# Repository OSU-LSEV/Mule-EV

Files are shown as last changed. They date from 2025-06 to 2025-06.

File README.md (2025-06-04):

# Mule-EV
Modified iteration of the woodpecker EV platform 

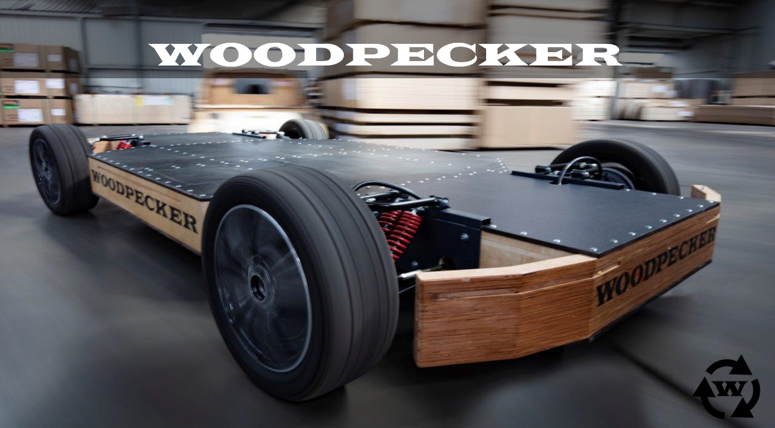
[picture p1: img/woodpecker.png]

# Woodpecker 
## Design documentation and Operating Manual
The main information backboan is CAN bus.

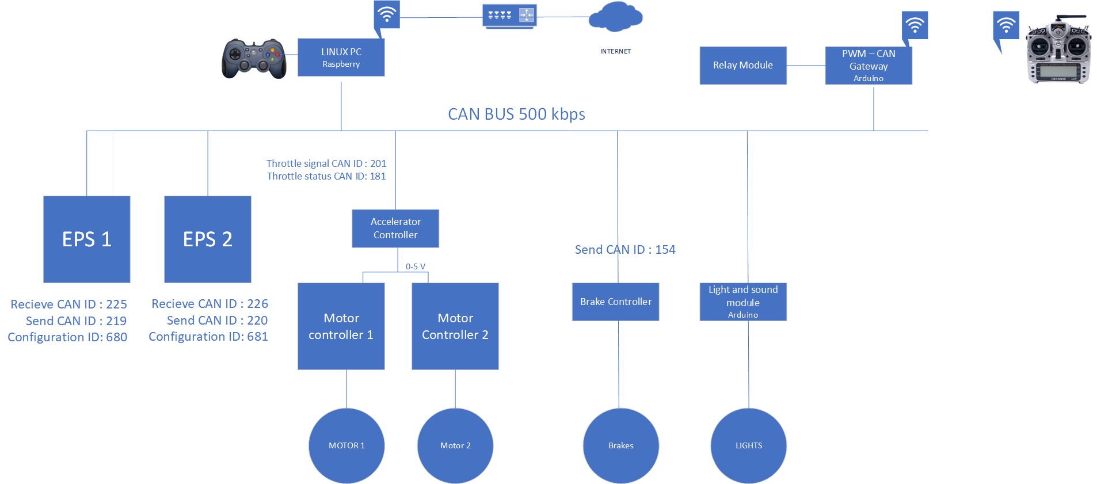
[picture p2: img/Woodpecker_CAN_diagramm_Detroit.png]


# Operation
There are 2 operating modes: manual and DbW mode. 
Wireless operations:

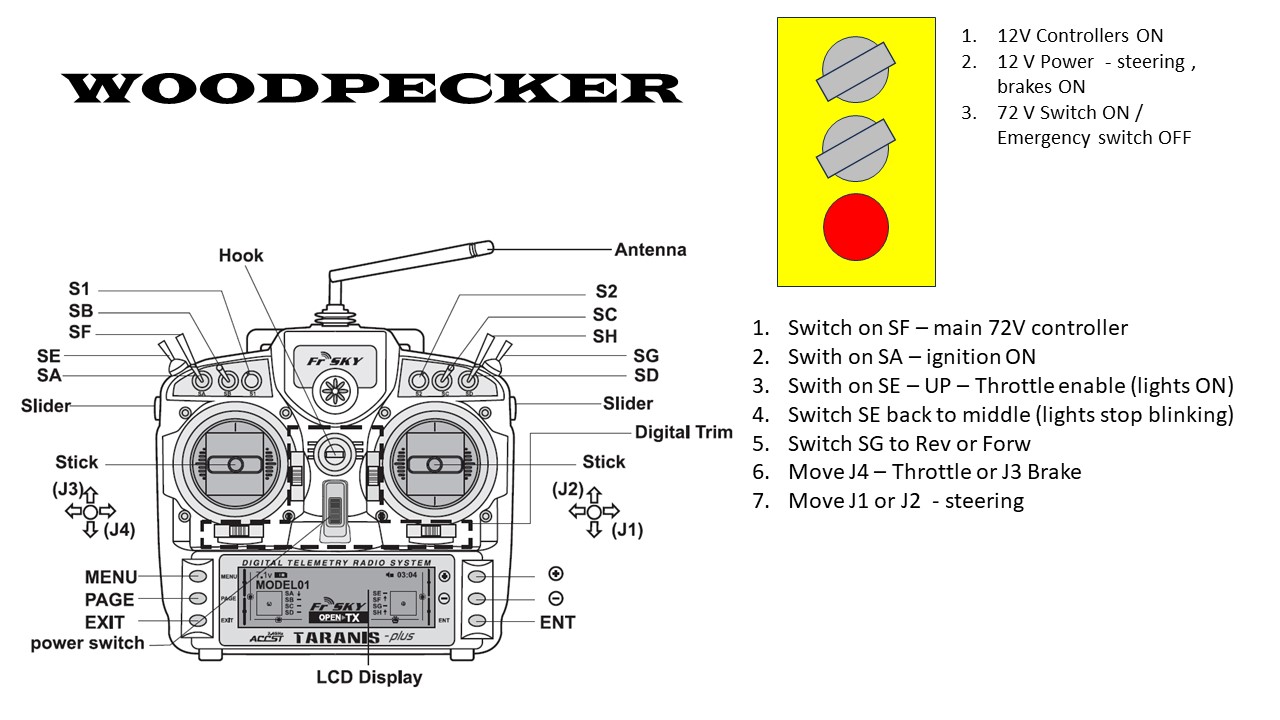
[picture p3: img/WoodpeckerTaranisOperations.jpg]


## Switching ON DbW mode

1. Switch DbW ON switch on front panel. Red signal light must light on. [Make sure mushroom Emergency STOP is released]
2. Wait for 30-50 sec to boot up Joystick micro computer. Joystick demo application should startup automatically.
3. Press START on joystick controller [Should hear clicking noise of controller relays] to enable controller.
4. Press Y to switch on ignition. Wait for 2-3 sec.
5. Press B to start starter.
6. Use joystick controls to drive, manually switch into high or low gear.

# Main DbW components.

Drive By Wire system consists from:

**1. Accelerator Controller**

Connected to motor controller. Receive commands and provide report via DbW CAN messages. Located in Rigt side. 

**2. Brake Controller.**

Connected to hydraulic brake unit. Receive commands and provide report via DbW CAN messages. Located in Middle

**3. Control Processor.**

Control processor is connected to DbW CAN network and 4 relay block and 2 push button switches to provide Engine ON, OFF and override functionality. Located in Right side 

**4. Joystick micro computer**

Raspberry Pi micro computer is located in Right side of vehicle, Logitech F310 gamepad attached via USB port. Connected to DbW CAN and LAN port on front panel. Joystick sample application is located on microcomputer dir /home/pi/Razor .
Bash script fro automatic joystick launch is located @ /home/pi/dbwstart.sh
Script is being launched on bootup from config file /etc/rc.local

content of .dbstart.sh script:
```
#!/bin/bash

sudo ip link set can0 type can bitrate 500000
sudo ip link set up can0
sudo ip link set can1 type can bitrate 500000
sudo ip link set up can1
cd /home/pi/Razor/build
./oscc-joystick-commander 0
```

Access information:
```
Connect using SSH to 10.0.10.15:22
User: pi
Password: nvidia
```

# CAN buse
There are 1 CAN buses on vehicle. DbW CAN screw terminal is located in Right side.

1. DbW CAN bus. - 500k

Connected devices: Brake controller, Accelerator controller, Steering controller, CAN Gateway, 

# Controls

1. DbW ON - Main Power switch ON/OFF. Power up all controllers. If Switched OFF DbW is disabled, fall back to manual.
2. Emergency STOP - DbW switch off. If pressed, DbW controls disabled, switch back to manual mode. Connected in Parallel with DbW ON switch.
3. LAN Connection - LAN port to connect to Joystick micro computer.
4. Power Steer ON - Button to force steering unit to switch ON power assist mode.

## Joystick operation

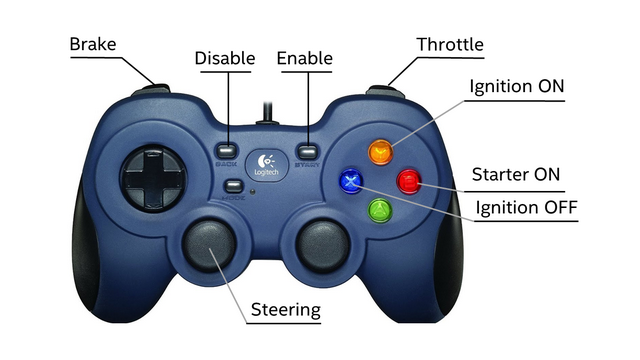
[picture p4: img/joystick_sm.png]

```
START - Enable controls
BACK - Disable controls
LEFT TRIGGER - Brake
RIGHT TRIGGER - Throttle
LEFT STICK - Steering
Y - Ignition ON
X - Ignition OFF
B - Starter ON
```
## CAN Modem

System is using PEAK CAN USB modem.
Drivers are available from Peak Systems website : https://www.peak-system.com/PCAN-USB.199.0.html?L=1# 
Connection port connector is located in the front panel of 
Pin out diagram is here:

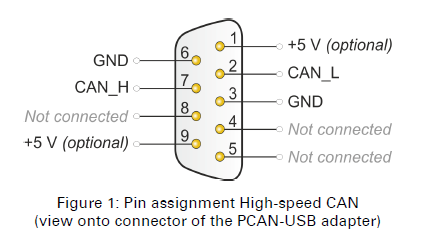
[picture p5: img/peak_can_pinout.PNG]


# Operation from management computer with joystick application:

In order to start operations of DbW:

1.	Switch main power switch On.
2.	Wait 1-2 min to start all processors.
3.	Initiate joystick controller (for test mode only). Connect to DbW GW controller from management PC:
a.	Launch Putty;
b.	Enter SSH connection to 10.0.10.15 
c.	Launch 1st  test window to monitor accelerator/braking signal:
d.	Enter username : pi
e.	Enter password: nvidia

```
cd /home/pi/can-utils
./candump can1
```
f.	As result the realtime changing data should appear:
```
  can1  061   [8]  05 CC 01 00 00 0F 00 01
  can1  063   [8]  05 CC 01 00 00 F2 08 08
  can1  061   [8]  05 CC 01 00 00 0F 00 01
  can1  063   [8]  05 CC 01 00 00 40 02 06
```

If there are no realtime data – DbW CAN interface is down, See troubleshooting.

k.	Launch 2nd Putty Window for joystick commander: 
cd /home/pi/Razor/build
./oscc-joystick-commander 0       

l.	There should be visible initiating screen – similar to: 
```
Opening EPAS CAN channel: can0
Opening CAN channel: can1
Found 1 devices -- connecting to device at system index 0 - GUID:030000006d0400001dc2000014400000
Waiting for joystick controls to zero
Joystick controls successfully initialized

Control Ready:
    START - Enable controls
    BACK - Disable controls
    LEFT TRIGGER - Brake
    RIGHT TRIGGER - Throttle
    LEFT STICK - Steering
```
m.	Press “START” to Enable controls, press “BACK” to Disable controls
n.	Controls on Joystick:     LEFT TRIGGER – Brake; RIGHT TRIGGER – Throttle ; LEFT STICK - Steering
o.	Typical view of DbW interface:
```
Brake: 0.000000 Throttle: 0.950990 Steering bytes: 0000
Brake: 0.000000 Throttle: 0.920007 Steering bytes: 0000
```
4.	Switch on ignition.
5.  Start the Engine
5.	Manually switch in to gear
7.	Start driving with joystick control

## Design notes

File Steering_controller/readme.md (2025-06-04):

# Woodpecker 
## Steering controller

PILOT SBW2 EPS is Drive-by-wire electric power steering (EPS) system

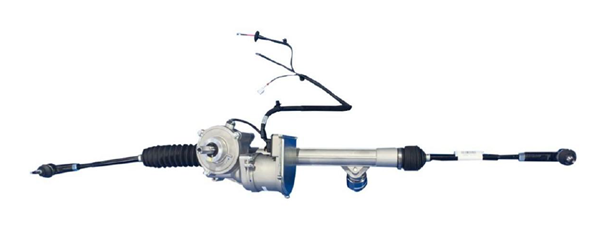
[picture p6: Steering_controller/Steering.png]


Steering module is used to convert CAN message to steering angle.
Module is configured to operate on 500Kbps baudrate.

The message is used in: https://github.com/OSU-LSEV/Mule-EV/blob/main/PWM_CAN_gateway/Woodpecker_PWM_CAN_GTW_Oregon/Woodpecker_PWM_CAN_GTW_Oregon.ino

Mapping of important CAN commandes from CAN .dbc files : https://bitbucket.org/pilotautomotive/woodpecker-detroit-documentation/src/master/CAN_docs/Woodpecker_Detroit.DBF  
```
StatusEPS1: 0x225
StatusEPS2: 0x226
CommandEPS1: 0x219
CommandEPS2: 0x220

```
Calculations of steering applied as CAN DEC to HEX messages are here: https://github.com/OSU-LSEV/Mule-EV/blob/main/Steering_controller/EPS_CAN_messages_calculation.xlsx and here https://github.com/OSU-LSEV/Mule-EV/blob/main/Steering_controller/Steering_joystick_commands.xlsx 
The final predifined messages from https://github.com/OSU-LSEV/Mule-EV/blob/main/PWM_CAN_gateway/Woodpecker_PWM_CAN_GTW_Oregon/Woodpecker_PWM_CAN_GTW_Oregon.ino  remote control look like:
```
unsigned char steer20[8] = {0x40, 0xFA, 0xCF, 0x39, 0x00, 0x00, 0x00, 0x00};
unsigned char steer19[8] = {0x40, 0xFA, 0x71, 0x38, 0x00, 0x00, 0x00, 0x00};
unsigned char steer18[8] = {0x40, 0xFA, 0x13, 0x37, 0x00, 0x00, 0x00, 0x00};
unsigned char steer17[8] = {0x40, 0xFA, 0xB5, 0x35, 0x00, 0x00, 0x00, 0x00};
unsigned char steer16[8] = {0x40, 0xFA, 0x57, 0x34, 0x00, 0x00, 0x00, 0x00};
unsigned char steer15[8] = {0x40, 0xFA, 0xF9, 0x32, 0x00, 0x00, 0x00, 0x00};
unsigned char steer14[8] = {0x40, 0xFA, 0x9B, 0x31, 0x00, 0x00, 0x00, 0x00};
unsigned char steer13[8] = {0x40, 0xFA, 0x3D, 0x30, 0x00, 0x00, 0x00, 0x00};
unsigned char steer12[8] = {0x40, 0xFA, 0xDF, 0x2E, 0x00, 0x00, 0x00, 0x00};
unsigned char steer11[8] = {0x40, 0xFA, 0x81, 0x2D, 0x00, 0x00, 0x00, 0x00};
unsigned char steer10[8] = {0x40, 0xFA, 0x23, 0x2C, 0x00, 0x00, 0x00, 0x00};
unsigned char steer9[8] = {0x40, 0xFA, 0xC5, 0x2A, 0x00, 0x00, 0x00, 0x00};
unsigned char steer8[8] = {0x40, 0xFA, 0x67, 0x29, 0x00, 0x00, 0x00, 0x00};
unsigned char steer7[8] = {0x40, 0xFA, 0x09, 0x28, 0x00, 0x00, 0x00, 0x00};
unsigned char steer6[8] = {0x40, 0xFA, 0xAB, 0x26, 0x00, 0x00, 0x00, 0x00};
unsigned char steer5[8] = {0x40, 0xFA, 0x4D, 0x25, 0x00, 0x00, 0x00, 0x00};
unsigned char steer4[8] = {0x40, 0xFA, 0xEF, 0x23, 0x00, 0x00, 0x00, 0x00};
unsigned char steer3[8] = {0x40, 0xFA, 0x91, 0x22, 0x00, 0x00, 0x00, 0x00};
unsigned char steer2[8] = {0x40, 0xFA, 0x33, 0x21, 0x00, 0x00, 0x00, 0x00};
unsigned char steer1[8] = {0x40, 0xFA, 0xD5, 0x1F, 0x00, 0x00, 0x00, 0x00};
unsigned char steer0[8] = {0x40, 0xFA, 0x77, 0x1E, 0x00, 0x00, 0x00, 0x00};
unsigned char steern1[8] = {0x40, 0xFA, 0x19, 0x1D, 0x00, 0x00, 0x00, 0x00};
unsigned char steern2[8] = {0x40, 0xFA, 0xBB, 0x1B, 0x00, 0x00, 0x00, 0x00};
unsigned char steern3[8] = {0x40, 0xFA, 0x5D, 0x1A, 0x00, 0x00, 0x00, 0x00};
unsigned char steern4[8] = {0x40, 0xFA, 0xFF, 0x18, 0x00, 0x00, 0x00, 0x00};
unsigned char steern5[8] = {0x40, 0xFA, 0xA1, 0x17, 0x00, 0x00, 0x00, 0x00};
unsigned char steern6[8] = {0x40, 0xFA, 0x43, 0x16, 0x00, 0x00, 0x00, 0x00};
unsigned char steern7[8] = {0x40, 0xFA, 0xE5, 0x14, 0x00, 0x00, 0x00, 0x00};
unsigned char steern8[8] = {0x40, 0xFA, 0x87, 0x13, 0x00, 0x00, 0x00, 0x00};
unsigned char steern9[8] = {0x40, 0xFA, 0x29, 0x12, 0x00, 0x00, 0x00, 0x00};
unsigned char steern10[8] = {0x40, 0xFA, 0xCB, 0x10, 0x00, 0x00, 0x00, 0x00};
unsigned char steern11[8] = {0x40, 0xFA, 0x6D, 0x0F, 0x00, 0x00, 0x00, 0x00};
unsigned char steern12[8] = {0x40, 0xFA, 0x0F, 0x0E, 0x00, 0x00, 0x00, 0x00};
unsigned char steern13[8] = {0x40, 0xFA, 0xB1, 0x0C, 0x00, 0x00, 0x00, 0x00};
unsigned char steern14[8] = {0x40, 0xFA, 0x53, 0x0B, 0x00, 0x00, 0x00, 0x00};
unsigned char steern15[8] = {0x40, 0xFA, 0xF5, 0x09, 0x00, 0x00, 0x00, 0x00};
unsigned char steern16[8] = {0x40, 0xFA, 0x97, 0x08, 0x00, 0x00, 0x00, 0x00};
unsigned char steern17[8] = {0x40, 0xFA, 0x38, 0x07, 0x00, 0x00, 0x00, 0x00};
unsigned char steern18[8] = {0x40, 0xFA, 0xDA, 0x05, 0x00, 0x00, 0x00, 0x00};
unsigned char steern19[8] = {0x40, 0xFA, 0x7C, 0x04, 0x00, 0x00, 0x00, 0x00};
unsigned char steern20[8] = {0x40, 0xFA, 0x1E, 0x03, 0x00, 0x00, 0x00, 0x00};
```

and

```
if (ch1 > 980 && ch1 < 1105) {CAN.sendMsgBuf(0x219, 0, 8, steern20);Serial.println(-20);};
  if (ch1 > 1106 && ch1 < 1125) {CAN.sendMsgBuf(0x219, 0, 8, steern19);Serial.println(-19);};
  if (ch1 > 1126 && ch1 < 1145) {CAN.sendMsgBuf(0x219, 0, 8, steern18);Serial.println(-18);};
  if (ch1 > 1146 && ch1 < 1165) {CAN.sendMsgBuf(0x219, 0, 8, steern17);Serial.println(-17);};
  if (ch1 > 1166 && ch1 < 1185) {CAN.sendMsgBuf(0x219, 0, 8, steern16);Serial.println(-16);};
  if (ch1 > 1186 && ch1 < 1205) {CAN.sendMsgBuf(0x219, 0, 8, steern15);Serial.println(-15);};
  if (ch1 > 1206 && ch1 < 1225) {CAN.sendMsgBuf(0x219, 0, 8, steern14);Serial.println(-14);};
  if (ch1 > 1226 && ch1 < 1245) {CAN.sendMsgBuf(0x219, 0, 8, steern13);Serial.println(-13);};
  if (ch1 > 1246 && ch1 < 1265) {CAN.sendMsgBuf(0x219, 0, 8, steern12);Serial.println(-12);};
  if (ch1 > 1266 && ch1 < 1285) {CAN.sendMsgBuf(0x219, 0, 8, steern11);Serial.println(-11);};
  if (ch1 > 1286 && ch1 < 1305) {CAN.sendMsgBuf(0x219, 0, 8, steern10);Serial.println(-10);};
  if (ch1 > 1306 && ch1 < 1325) {CAN.sendMsgBuf(0x219, 0, 8, steern9);Serial.println(-9);};
  if (ch1 > 1326 && ch1 < 1345) {CAN.sendMsgBuf(0x219, 0, 8, steern8);Serial.println(-8);};
  if (ch1 > 1346 && ch1 < 1365) {CAN.sendMsgBuf(0x219, 0, 8, steern7);Serial.println(-7);};
  if (ch1 > 1366 && ch1 < 1385) {CAN.sendMsgBuf(0x219, 0, 8, steern6);Serial.println(-6);};
  if (ch1 > 1386 && ch1 < 1405) {CAN.sendMsgBuf(0x219, 0, 8, steern5);Serial.println(-5);};
  if (ch1 > 1406 && ch1 < 1425) {CAN.sendMsgBuf(0x219, 0, 8, steern4);Serial.println(-4);};
  if (ch1 > 1426 && ch1 < 1445) {CAN.sendMsgBuf(0x219, 0, 8, steern3);Serial.println(-3);};
  if (ch1 > 1446 && ch1 < 1465) {CAN.sendMsgBuf(0x219, 0, 8, steern2);Serial.println(-2);};
  if (ch1 > 1466 && ch1 < 1479) {CAN.sendMsgBuf(0x219, 0, 8, steer0);Serial.println(-1);};
  if (ch1 > 1480 && ch1 < 1505) {CAN.sendMsgBuf(0x219, 0, 8, steer0);Serial.println(0);};
  if (ch1 > 1506 && ch1 < 1525) {CAN.sendMsgBuf(0x219, 0, 8, steer0);Serial.println(1);};
  if (ch1 > 1526 && ch1 < 1545) {CAN.sendMsgBuf(0x219, 0, 8, steer2);Serial.println(2);};
  if (ch1 > 1546 && ch1 < 1565) {CAN.sendMsgBuf(0x219, 0, 8, steer3);Serial.println(3);};
  if (ch1 > 1566 && ch1 < 1585) {CAN.sendMsgBuf(0x219, 0, 8, steer4);Serial.println(4);};
  if (ch1 > 1586 && ch1 < 1605) {CAN.sendMsgBuf(0x219, 0, 8, steer5);Serial.println(5);};
  if (ch1 > 1606 && ch1 < 1625) {CAN.sendMsgBuf(0x219, 0, 8, steer6);Serial.println(6);};
  if (ch1 > 1626 && ch1 < 1645) {CAN.sendMsgBuf(0x219, 0, 8, steer7);Serial.println(7);};
  if (ch1 > 1646 && ch1 < 1665) {CAN.sendMsgBuf(0x219, 0, 8, steer8);Serial.println(8);};
  if (ch1 > 1666 && ch1 < 1685) {CAN.sendMsgBuf(0x219, 0, 8, steer9);Serial.println(9);};
  if (ch1 > 1686 && ch1 < 1705) {CAN.sendMsgBuf(0x219, 0, 8, steer10);Serial.println(10);};
  if (ch1 > 1706 && ch1 < 1725) {CAN.sendMsgBuf(0x219, 0, 8, steer11);Serial.println(11);};
  if (ch1 > 1726 && ch1 < 1745) {CAN.sendMsgBuf(0x219, 0, 8, steer12);Serial.println(12);};
  if (ch1 > 1746 && ch1 < 1765) {CAN.sendMsgBuf(0x219, 0, 8, steer13);Serial.println(13);};
  if (ch1 > 1766 && ch1 < 1785) {CAN.sendMsgBuf(0x219, 0, 8, steer14);Serial.println(14);};
  if (ch1 > 1786 && ch1 < 1805) {CAN.sendMsgBuf(0x219, 0, 8, steer15);Serial.println(15);};
  if (ch1 > 1806 && ch1 < 1825) {CAN.sendMsgBuf(0x219, 0, 8, steer16);Serial.println(16);};
  if (ch1 > 1826 && ch1 < 1845) {CAN.sendMsgBuf(0x219, 0, 8, steer17);Serial.println(17);};
  if (ch1 > 1846 && ch1 < 1865) {CAN.sendMsgBuf(0x219, 0, 8, steer18);Serial.println(18);};
  if (ch1 > 1866 && ch1 < 1885) {CAN.sendMsgBuf(0x219, 0, 8, steer19);Serial.println(19);};
  if (ch1 > 1886 && ch1 < 2005) {CAN.sendMsgBuf(0x219, 0, 8, steer19);Serial.println(20);};

if (ch3 > 1000 && ch3 < 1189) CAN.sendMsgBuf(0x220, 0, 8, steern20);
if (ch3 > 1190 && ch3 < 1209) CAN.sendMsgBuf(0x220, 0, 8, steern19);
if (ch3 > 1210 && ch3 < 1229) CAN.sendMsgBuf(0x220, 0, 8, steern18);
if (ch3 > 1230 && ch3 < 1249) CAN.sendMsgBuf(0x220, 0, 8, steern17);
if (ch3 > 1250 && ch3 < 1269) CAN.sendMsgBuf(0x220, 0, 8, steern16);
if (ch3 > 1270 && ch3 < 1289) CAN.sendMsgBuf(0x220, 0, 8, steern15);
if (ch3 > 1290 && ch3 < 1309) CAN.sendMsgBuf(0x220, 0, 8, steern14);
if (ch3 > 1310 && ch3 < 1329) CAN.sendMsgBuf(0x220, 0, 8, steern13);
if (ch3 > 1330 && ch3 < 1349) CAN.sendMsgBuf(0x220, 0, 8, steern12);
if (ch3 > 1350 && ch3 < 1369) CAN.sendMsgBuf(0x220, 0, 8, steern11);
if (ch3 > 1370 && ch3 < 1389) CAN.sendMsgBuf(0x220, 0, 8, steern10);
if (ch3 > 1390 && ch3 < 1409) CAN.sendMsgBuf(0x220, 0, 8, steern9);
if (ch3 > 1410 && ch3 < 1429) CAN.sendMsgBuf(0x220, 0, 8, steern8);
if (ch3 > 1430 && ch3 < 1449) CAN.sendMsgBuf(0x220, 0, 8, steern7);
if (ch3 > 1450 && ch3 < 1469) CAN.sendMsgBuf(0x220, 0, 8, steern6);
if (ch3 > 1470 && ch3 < 1489) CAN.sendMsgBuf(0x220, 0, 8, steern5);
if (ch3 > 1490 && ch3 < 1509) CAN.sendMsgBuf(0x220, 0, 8, steern4);
if (ch3 > 1510 && ch3 < 1529) CAN.sendMsgBuf(0x220, 0, 8, steern3);
if (ch3 > 1530 && ch3 < 1549) CAN.sendMsgBuf(0x220, 0, 8, steern2);
if (ch3 > 1550 && ch3 < 1569) CAN.sendMsgBuf(0x220, 0, 8, steern1);
if (ch3 > 1570 && ch3 < 1590) CAN.sendMsgBuf(0x220, 0, 8, steer0);
if (ch3 > 1591 && ch3 < 1610) CAN.sendMsgBuf(0x220, 0, 8, steer1);
if (ch3 > 1611 && ch3 < 1630) CAN.sendMsgBuf(0x220, 0, 8, steer2);
if (ch3 > 1631 && ch3 < 1650) CAN.sendMsgBuf(0x220, 0, 8, steer3);
if (ch3 > 1651 && ch3 < 1670) CAN.sendMsgBuf(0x220, 0, 8, steer4);
if (ch3 > 1671 && ch3 < 1690) CAN.sendMsgBuf(0x220, 0, 8, steer5);
if (ch3 > 1691 && ch3 < 1710) CAN.sendMsgBuf(0x220, 0, 8, steer6);
if (ch3 > 1711 && ch3 < 1730) CAN.sendMsgBuf(0x220, 0, 8, steer7);
if (ch3 > 1731 && ch3 < 1750) CAN.sendMsgBuf(0x220, 0, 8, steer8);
if (ch3 > 1751 && ch3 < 1770) CAN.sendMsgBuf(0x220, 0, 8, steer9);
if (ch3 > 1771 && ch3 < 1790) CAN.sendMsgBuf(0x220, 0, 8, steer10);
if (ch3 > 1791 && ch3 < 1810) CAN.sendMsgBuf(0x220, 0, 8, steer11);
if (ch3 > 1811 && ch3 < 1830) CAN.sendMsgBuf(0x220, 0, 8, steer12);
if (ch3 > 1831 && ch3 < 1850) CAN.sendMsgBuf(0x220, 0, 8, steer13);
if (ch3 > 1851 && ch3 < 1870) CAN.sendMsgBuf(0x220, 0, 8, steer14);
if (ch3 > 1871 && ch3 < 1890) CAN.sendMsgBuf(0x220, 0, 8, steer15);
if (ch3 > 1891 && ch3 < 1910) CAN.sendMsgBuf(0x220, 0, 8, steer16);
if (ch3 > 1911 && ch3 < 1930) CAN.sendMsgBuf(0x220, 0, 8, steer17);
if (ch3 > 1931 && ch3 < 1950) CAN.sendMsgBuf(0x220, 0, 8, steer18);
if (ch3 > 1951 && ch3 < 2010) CAN.sendMsgBuf(0x220, 0, 8, steer19);
```

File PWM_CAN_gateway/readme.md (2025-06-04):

# Woodpecker 
## PWM CAN Gateway

Woodpecker PWM CAN Gateway is custom made Arduino based system with CAN external shield and relay module.
Module consist from: 

1. Arduino Due Mega2560 R3 JOY-IT ARD-Mega2560R3 https://docs.arduino.cc/hardware/due/
2. SeedStudio CAN shield https://wiki.seeedstudio.com/CAN-BUS_Shield_V2.0/
3. 8 Relay Module 
4. Taranis Remote module

The module operates:
1. Recieving the radio commands from Tarranis remote in up to 8 channels;
2. Converts recieved PWM values to CAN messages for steering, braking, acceleration regardig the code;
3. Converts PWM signals to signals for switching the relays on or off - Ķey On", Reverse/Forward.

The logics of operation is easy readable in comments in ARduino scetch code: 
https://github.com/OSU-LSEV/Mule-EV/blob/main/PWM_CAN_gateway/Woodpecker_PWM_CAN_GTW_Oregon/Woodpecker_PWM_CAN_GTW_Oregon.ino

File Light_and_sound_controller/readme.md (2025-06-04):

# Woodpecker 
## Sound and light controller

Woodpecker Sound and light controller is custom made Arduino based system with CAN extarnal board and relay module.
Module consist from: 

1. Arduino Due Mega2560 R3 JOY-IT ARD-Mega2560R3 https://docs.arduino.cc/hardware/due/
2. SeedStudio CAN shield https://wiki.seeedstudio.com/CAN-BUS_Shield_V2.0/
3. 8 Relay Module 

External illunination is done by 6 WS2812B LED strips

Module is operating in 2 ways:
```
1. Prerecorded sequence of illuminations
2. Different signals when connected to CAN and recieve CAN signals (like turns or brakes).
```
The module operates:
1. Led light strips for signal lights;
2. Relays for optional stiop, blinker lamps and headlights;
3. Horn.

The logics of operation is easy readable in comments in ARduino scetch code: https://github.com/OSU-LSEV/Mule-EV/blob/main/Light_and_sound_controller/LED_woodpecker_final_2023_Oregon/LED_woodpecker_final_2023_Oregon.ino

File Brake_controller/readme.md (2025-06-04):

# Woodpecker 
## Brake controller

PILOT DBS or Dynamic Brake System is Drive-by-wire electronic hydraulic brake system

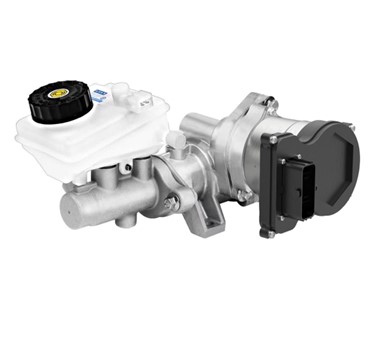
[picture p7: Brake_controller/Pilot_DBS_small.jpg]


Brake nodule is used to convert CAN message to hydrolic braking power.
Module is configured to operatro on 500Kbps baudrate.

The message is used in: https://github.com/OSU-LSEV/Mule-EV/blob/main/PWM_CAN_gateway/Woodpecker_PWM_CAN_GTW_Oregon/Woodpecker_PWM_CAN_GTW_Oregon.ino

Mapping of important CAN commandes from CAN .dbc files : https://github.com/OSU-LSEV/Mule-EV/blob/main/CAN_docs/Woodpecker_Oregon.DBF  and https://github.com/OSU-LSEV/Mule-EV/blob/main/CAN_docs/DBS3001_231010.dbf 
```
CommandBrake: 0x154
BrakeErrorMessage: 0x143
BrakeStatusMessage: 0x142

```
Calculations of hydrolic power applied vs CAN DEC to HEX messages are here: https://github.com/OSU-LSEV/Mule-EV/blob/main/Brake_controller/DBS_CAN_messages_calculations.xlsx The final predifined messages from https://github.com/OSU-LSEV/Mule-EV/blob/main/PWM_CAN_gateway/Woodpecker_PWM_CAN_GTW_Oregon/Woodpecker_PWM_CAN_GTW_Oregon.ino   remote control look like:
```
unsigned char brake1[8] = {0x01, 0x00, 0x00, 0x00, 0x00, 0x00, 0x00, 0x00};
unsigned char brake2[8] = {0x01, 0x00, 0x05, 0x00, 0x00, 0x00, 0x00, 0x00};
unsigned char brake3[8] = {0x01, 0x00, 0x0A, 0x00, 0x00, 0x00, 0x00, 0x00};
unsigned char brake4[8] = {0x01, 0x00, 0x0F, 0x00, 0x00, 0x00, 0x00, 0x00};
unsigned char brake5[8] = {0x01, 0x00, 0x14, 0x00, 0x00, 0x00, 0x00, 0x00};
unsigned char brake6[8] = {0x01, 0x00, 0x19, 0x00, 0x00, 0x00, 0x00, 0x00};
unsigned char brake7[8] = {0x01, 0x00, 0x1E, 0x00, 0x00, 0x00, 0x00, 0x00};
unsigned char brake8[8] = {0x01, 0x00, 0x23, 0x00, 0x00, 0x00, 0x00, 0x00};
unsigned char brake9[8] = {0x01, 0x00, 0x28, 0x00, 0x00, 0x00, 0x00, 0x00};
unsigned char brake10[8] = {0x01, 0x00, 0x2D, 0x00, 0x00, 0x00, 0x00, 0x00};
unsigned char brake11[8] = {0x01, 0x00, 0x32, 0x00, 0x00, 0x00, 0x00, 0x00};
unsigned char brake12[8] = {0x01, 0x00, 0x37, 0x00, 0x00, 0x00, 0x00, 0x00};
unsigned char brake13[8] = {0x01, 0x00, 0x3C, 0x00, 0x00, 0x00, 0x00, 0x00};
unsigned char brake14[8] = {0x01, 0x00, 0x41, 0x00, 0x00, 0x00, 0x00, 0x00};
unsigned char brake15[8] = {0x01, 0x00, 0x46, 0x00, 0x00, 0x00, 0x00, 0x00};
unsigned char brake16[8] = {0x01, 0x00, 0x4B, 0x00, 0x00, 0x00, 0x00, 0x00};
unsigned char brake17[8] = {0x01, 0x00, 0x50, 0x00, 0x00, 0x00, 0x00, 0x00};
unsigned char brake18[8] = {0x01, 0x00, 0x55, 0x00, 0x00, 0x00, 0x00, 0x00};
unsigned char brake19[8] = {0x01, 0x00, 0x5A, 0x00, 0x00, 0x00, 0x00, 0x00};
unsigned char brake20[8] = {0x01, 0x00, 0x5F, 0x00, 0x00, 0x00, 0x00, 0x00};
unsigned char brake21[8] = {0x01, 0x00, 0x64, 0x00, 0x00, 0x00, 0x00, 0x00};
```

and

```
if (ch8<1550 && ch8>1400){ CAN.sendMsgBuf(0x154, 0, 8, brake1);Serial.println("BR1");};
if (ch8<1399 && ch8>1378){ CAN.sendMsgBuf(0x154, 0, 8, brake2);Serial.println("BR2");};
if (ch8<1377 && ch8>1356){ CAN.sendMsgBuf(0x154, 0, 8, brake3);Serial.println("BR3");};
if (ch8<1355 && ch8>1334){ CAN.sendMsgBuf(0x154, 0, 8, brake4);Serial.println("BR4");};
if (ch8<1333 && ch8>1312){ CAN.sendMsgBuf(0x154, 0, 8, brake5);Serial.println("BR5");};
if (ch8<1311 && ch8>1290){ CAN.sendMsgBuf(0x154, 0, 8, brake6);Serial.println("BR6");};
if (ch8<1289 && ch8>1268){ CAN.sendMsgBuf(0x154, 0, 8, brake7);Serial.println("BR7");};
if (ch8<1267 && ch8>1246){ CAN.sendMsgBuf(0x154, 0, 8, brake8);Serial.println("BR8");};
if (ch8<1245 && ch8>1224){ CAN.sendMsgBuf(0x154, 0, 8, brake9);Serial.println("BR9");};
if (ch8<1223 && ch8>1202){ CAN.sendMsgBuf(0x154, 0, 8, brake10);Serial.println("BR10");};
if (ch8<1201 && ch8>1180){ CAN.sendMsgBuf(0x154, 0, 8, brake11);Serial.println("BR11");};
if (ch8<1179 && ch8>1158){ CAN.sendMsgBuf(0x154, 0, 8, brake12);Serial.println("BR12");};
if (ch8<1157 && ch8>1136){ CAN.sendMsgBuf(0x154, 0, 8, brake13);Serial.println("BR13");};
if (ch8<1135 && ch8>1114){ CAN.sendMsgBuf(0x154, 0, 8, brake14);Serial.println("BR14");};
if (ch8<1113 && ch8>1092){ CAN.sendMsgBuf(0x154, 0, 8, brake15);Serial.println("BR15");};
if (ch8<1091 && ch8>1070){ CAN.sendMsgBuf(0x154, 0, 8, brake16);Serial.println("BR16");};
if (ch8<1069 && ch8>1048){ CAN.sendMsgBuf(0x154, 0, 8, brake17);Serial.println("BR17");};
if (ch8<1047 && ch8>1026){ CAN.sendMsgBuf(0x154, 0, 8, brake18);Serial.println("BR18");};
if (ch8<1025 && ch8>1004){ CAN.sendMsgBuf(0x154, 0, 8, brake19);Serial.println("BR19");};
if (ch8<1003 && ch8>982){ CAN.sendMsgBuf(0x154, 0, 8, brake20);Serial.println("BR20");};
if (ch8<981 && ch8>980){ CAN.sendMsgBuf(0x154, 0, 8, brake21);Serial.println("BR21");};
```

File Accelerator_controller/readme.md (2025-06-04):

# Woodpecker 
## Accelerator controller

Accelerator controller PILOT ICAN is based on ICAN-4404 4-channel isolated analog output module.

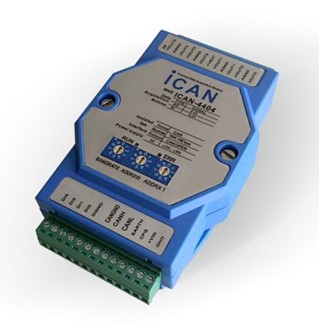
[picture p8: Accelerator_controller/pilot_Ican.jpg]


Accelerator module's function is to convert CAN messages to analog signal - voltage from 0-5 V necessary for motor controllers.
Module is configured to operatro on 500Kbps baudrate.

In order to start operations of module CAN message: 
0x00  01 01 00 00 00 00 00 00 should be sent
The message is used in: https://github.com/OSU-LSEV/Mule-EV/blob/main/PWM_CAN_gateway/Woodpecker_PWM_CAN_GTW_Oregon/Woodpecker_PWM_CAN_GTW_Oregon.ino

Mapping of important CAN commandes from CAN .dbc files : https://github.com/OSU-LSEV/Mule-EV/blob/main/CAN_docs/ican_4404_Woodpecker_Oregon.DBF
```
AcceleratorFeedback   0x701
Throttle_Status		  0x161
CommandThrottle		  0x201
Throttle Init Message 0x00
```
Calculations of voltage vs CAN DEC to HEX messages are here: https://github.com/OSU-LSEV/Mule-EV/blob/main/Steering_controller/RC_PWM_CAN_conversions_Oregon.xlsx
The final predifined messages from https://github.com/OSU-LSEV/Mule-EV/blob/main/PWM_CAN_gateway/Woodpecker_PWM_CAN_GTW_Oregon/Woodpecker_PWM_CAN_GTW_Oregon.ino remote control look like:
```
unsigned char accel0[8] = {0x00, 0x00, 0x00, 0x00, 0x00, 0x00, 0x00, 0x00};
unsigned char accel1[8] = {0x2E, 0x00, 0x00, 0x00, 0x00, 0x00, 0x00, 0x00};
unsigned char accel2[8] = {0x5C, 0x00, 0x00, 0x00, 0x00, 0x00, 0x00, 0x00};
unsigned char accel3[8] = {0x8A, 0x00, 0x00, 0x00, 0x00, 0x00, 0x00, 0x00};
unsigned char accel4[8] = {0xB8, 0x00, 0x00, 0x00, 0x00, 0x00, 0x00, 0x00};
unsigned char accel5[8] = {0xE6, 0x00, 0x00, 0x00, 0x00, 0x00, 0x00, 0x00};
unsigned char accel6[8] = {0x14, 0x01, 0x00, 0x00, 0x00, 0x00, 0x00, 0x00};
unsigned char accel7[8] = {0x42, 0x01, 0x00, 0x00, 0x00, 0x00, 0x00, 0x00};
unsigned char accel8[8] = {0x70, 0x01, 0x00, 0x00, 0x00, 0x00, 0x00, 0x00};
unsigned char accel9[8] = {0x9E, 0x01, 0x00, 0x00, 0x00, 0x00, 0x00, 0x00};
unsigned char accel10[8] = {0xCC, 0x01, 0x00, 0x00, 0x00, 0x00, 0x00, 0x00};
unsigned char accel11[8] = {0xFA, 0x01, 0x00, 0x00, 0x00, 0x00, 0x00, 0x00};
unsigned char accel12[8] = {0x28, 0x02, 0x00, 0x00, 0x00, 0x00, 0x00, 0x00};
unsigned char accel13[8] = {0x56, 0x02, 0x00, 0x00, 0x00, 0x00, 0x00, 0x00};
unsigned char accel14[8] = {0x84, 0x02, 0x00, 0x00, 0x00, 0x00, 0x00, 0x00};
unsigned char accel15[8] = {0xB2, 0x02, 0x00, 0x00, 0x00, 0x00, 0x00, 0x00};
unsigned char accel16[8] = {0xE0, 0x02, 0x00, 0x00, 0x00, 0x00, 0x00, 0x00};
unsigned char accel17[8] = {0x0E, 0x03, 0x00, 0x00, 0x00, 0x00, 0x00, 0x00};
unsigned char accel18[8] = {0x3C, 0x03, 0x00, 0x00, 0x00, 0x00, 0x00, 0x00};
unsigned char accel19[8] = {0x6A, 0x03, 0x00, 0x00, 0x00, 0x00, 0x00, 0x00};
unsigned char accel20[8] = {0x98, 0x03, 0x00, 0x00, 0x00, 0x00, 0x00, 0x00};
unsigned char accel21[8] = {0xC6, 0x03, 0x00, 0x00, 0x00, 0x00, 0x00, 0x00};
unsigned char accel22[8] = {0xF4, 0x03, 0x00, 0x00, 0x00, 0x00, 0x00, 0x00};
unsigned char accel23[8] = {0x22, 0x04, 0x00, 0x00, 0x00, 0x00, 0x00, 0x00};
unsigned char accel24[8] = {0x50, 0x04, 0x00, 0x00, 0x00, 0x00, 0x00, 0x00};
unsigned char accel25[8] = {0x7E, 0x04, 0x00, 0x00, 0x00, 0x00, 0x00, 0x00};
unsigned char accel26[8] = {0xAC, 0x04, 0x00, 0x00, 0x00, 0x00, 0x00, 0x00};
unsigned char accel27[8] = {0xDA, 0x04, 0x00, 0x00, 0x00, 0x00, 0x00, 0x00};
unsigned char accel28[8] = {0x08, 0x05, 0x00, 0x00, 0x00, 0x00, 0x00, 0x00};
unsigned char accel29[8] = {0x36, 0x05, 0x00, 0x00, 0x00, 0x00, 0x00, 0x00};
unsigned char accel30[8] = {0x64, 0x05, 0x00, 0x00, 0x00, 0x00, 0x00, 0x00};
unsigned char accel31[8] = {0x92, 0x05, 0x00, 0x00, 0x00, 0x00, 0x00, 0x00};
unsigned char accel32[8] = {0xC0, 0x05, 0x00, 0x00, 0x00, 0x00, 0x00, 0x00};
unsigned char accel33[8] = {0xEE, 0x05, 0x00, 0x00, 0x00, 0x00, 0x00, 0x00};
unsigned char accel34[8] = {0x1C, 0x06, 0x00, 0x00, 0x00, 0x00, 0x00, 0x00};
unsigned char accel35[8] = {0x4A, 0x06, 0x00, 0x00, 0x00, 0x00, 0x00, 0x00};
unsigned char accel36[8] = {0x78, 0x06, 0x00, 0x00, 0x00, 0x00, 0x00, 0x00};
unsigned char accel37[8] = {0xA6, 0x06, 0x00, 0x00, 0x00, 0x00, 0x00, 0x00};
unsigned char accel38[8] = {0xD4, 0x06, 0x00, 0x00, 0x00, 0x00, 0x00, 0x00};
unsigned char accel39[8] = {0x02, 0x07, 0x00, 0x00, 0x00, 0x00, 0x00, 0x00};
unsigned char accel40[8] = {0x30, 0x07, 0x00, 0x00, 0x00, 0x00, 0x00, 0x00};
unsigned char accel41[8] = {0x5E, 0x07, 0x00, 0x00, 0x00, 0x00, 0x00, 0x00};
unsigned char accel42[8] = {0x8C, 0x07, 0x00, 0x00, 0x00, 0x00, 0x00, 0x00};
unsigned char accel43[8] = {0xBA, 0x07, 0x00, 0x00, 0x00, 0x00, 0x00, 0x00};
unsigned char accel44[8] = {0xE8, 0x07, 0x00, 0x00, 0x00, 0x00, 0x00, 0x00};
unsigned char accel45[8] = {0xF8, 0x07, 0x00, 0x00, 0x00, 0x00, 0x00, 0x00};
unsigned char accel46[8] = {0xF8, 0x07, 0x00, 0x00, 0x00, 0x00, 0x00, 0x00};
```

and

```
if (ch2 > 950 && ch2 < 1011){ CAN.sendMsgBuf(0x201, 0, 8, accel1);Serial.println("TH1");}
else if (ch2 > 1012 && ch2 < 1033){ CAN.sendMsgBuf(0x201, 0, 8, accel2);Serial.println("TH2");}
else if (ch2 > 1034 && ch2 < 1055){ CAN.sendMsgBuf(0x201, 0, 8, accel3);Serial.println("TH3");}
else if (ch2 > 1056 && ch2 < 1077){ CAN.sendMsgBuf(0x201, 0, 8, accel4);Serial.println("TH4");}
else if (ch2 > 1078 && ch2 < 1099){ CAN.sendMsgBuf(0x201, 0, 8, accel5);Serial.println("TH5");}
else if (ch2 > 1100 && ch2 < 1121){ CAN.sendMsgBuf(0x201, 0, 8, accel6);Serial.println("TH6");}
else if (ch2 > 1122 && ch2 < 1143){ CAN.sendMsgBuf(0x201, 0, 8, accel7);Serial.println("TH7");}
else if (ch2 > 1144 && ch2 < 1165){ CAN.sendMsgBuf(0x201, 0, 8, accel8);Serial.println("TH8");}
else if (ch2 > 1166 && ch2 < 1187){ CAN.sendMsgBuf(0x201, 0, 8, accel9);Serial.println("TH9");}
else if (ch2 > 1188 && ch2 < 1209){ CAN.sendMsgBuf(0x201, 0, 8, accel10);Serial.println("TH10");}
else if (ch2 > 1210 && ch2 < 1231){ CAN.sendMsgBuf(0x201, 0, 8, accel11);Serial.println("TH11");}
else if (ch2 > 1232 && ch2 < 1253){ CAN.sendMsgBuf(0x201, 0, 8, accel12);Serial.println("TH12");}
else if (ch2 > 1254 && ch2 < 1275){ CAN.sendMsgBuf(0x201, 0, 8, accel13);Serial.println("TH13");}
else if (ch2 > 1276 && ch2 < 1297){ CAN.sendMsgBuf(0x201, 0, 8, accel14);Serial.println("TH14");}
else if (ch2 > 1298 && ch2 < 1319){ CAN.sendMsgBuf(0x201, 0, 8, accel15);Serial.println("TH15");}
else if (ch2 > 1320 && ch2 < 1341){ CAN.sendMsgBuf(0x201, 0, 8, accel16);Serial.println("TH16");}
else if (ch2 > 1342 && ch2 < 1363){ CAN.sendMsgBuf(0x201, 0, 8, accel17);Serial.println("TH17");}
else if (ch2 > 1364 && ch2 < 1385){ CAN.sendMsgBuf(0x201, 0, 8, accel18);Serial.println("TH18");}
else if (ch2 > 1386 && ch2 < 1407){ CAN.sendMsgBuf(0x201, 0, 8, accel19);Serial.println("TH19");}
else if (ch2 > 1408 && ch2 < 1429){ CAN.sendMsgBuf(0x201, 0, 8, accel20);Serial.println("TH20");}
else if (ch2 > 1430 && ch2 < 1451){ CAN.sendMsgBuf(0x201, 0, 8, accel21);Serial.println("TH21");}
else if (ch2 > 1452 && ch2 < 1473){ CAN.sendMsgBuf(0x201, 0, 8, accel22);Serial.println("TH22");}
else if (ch2 > 1474 && ch2 < 1495){ CAN.sendMsgBuf(0x201, 0, 8, accel23);Serial.println("TH23");}
else if (ch2 > 1496 && ch2 < 1517){ CAN.sendMsgBuf(0x201, 0, 8, accel24);Serial.println("TH24");}
else if (ch2 > 1518 && ch2 < 1539){ CAN.sendMsgBuf(0x201, 0, 8, accel25);Serial.println("TH25");}
else if (ch2 > 1540 && ch2 < 1561){ CAN.sendMsgBuf(0x201, 0, 8, accel26);Serial.println("TH26");}
else if (ch2 > 1562 && ch2 < 1583){ CAN.sendMsgBuf(0x201, 0, 8, accel27);Serial.println("TH27");}
else if (ch2 > 1584 && ch2 < 1605){ CAN.sendMsgBuf(0x201, 0, 8, accel28);Serial.println("TH28");}
else if (ch2 > 1606 && ch2 < 1627){ CAN.sendMsgBuf(0x201, 0, 8, accel29);Serial.println("TH29");}
else if (ch2 > 1628 && ch2 < 1649){ CAN.sendMsgBuf(0x201, 0, 8, accel30);Serial.println("TH30");}
else if (ch2 > 1650 && ch2 < 1671){ CAN.sendMsgBuf(0x201, 0, 8, accel31);Serial.println("TH31");}
else if (ch2 > 1672 && ch2 < 1693){ CAN.sendMsgBuf(0x201, 0, 8, accel32);Serial.println("TH32");}
else if (ch2 > 1694 && ch2 < 1715){ CAN.sendMsgBuf(0x201, 0, 8, accel33);Serial.println("TH33");}
else if (ch2 > 1716 && ch2 < 1737){ CAN.sendMsgBuf(0x201, 0, 8, accel34);Serial.println("TH34");}
else if (ch2 > 1738 && ch2 < 1759){ CAN.sendMsgBuf(0x201, 0, 8, accel35);Serial.println("TH35");}
else if (ch2 > 1760 && ch2 < 1781){ CAN.sendMsgBuf(0x201, 0, 8, accel36);Serial.println("TH36");}
else if (ch2 > 1782 && ch2 < 1803){ CAN.sendMsgBuf(0x201, 0, 8, accel37);Serial.println("TH37");}
else if (ch2 > 1804 && ch2 < 1825){ CAN.sendMsgBuf(0x201, 0, 8, accel38);Serial.println("TH38");}
else if (ch2 > 1826 && ch2 < 1847){ CAN.sendMsgBuf(0x201, 0, 8, accel39);Serial.println("TH39");}
else if (ch2 > 1848 && ch2 < 1869){ CAN.sendMsgBuf(0x201, 0, 8, accel40);Serial.println("TH40");}
else if (ch2 > 1870 && ch2 < 1891){ CAN.sendMsgBuf(0x201, 0, 8, accel41);Serial.println("TH41");}
else if (ch2 > 1892 && ch2 < 1913){ CAN.sendMsgBuf(0x201, 0, 8, accel42);Serial.println("TH42");}
else if (ch2 > 1914 && ch2 < 1935){ CAN.sendMsgBuf(0x201, 0, 8, accel43);Serial.println("TH43");}
else if (ch2 > 1936 && ch2 < 1957){ CAN.sendMsgBuf(0x201, 0, 8, accel44);Serial.println("TH44");}
else if (ch2 > 1958 && ch2 < 1979){ CAN.sendMsgBuf(0x201, 0, 8, accel45);Serial.println("TH45");}
else if (ch2 > 1980 && ch2 < 2100){ CAN.sendMsgBuf(0x201, 0, 8, accel46);Serial.println("TH46");}
else { CAN.sendMsgBuf(0x201, 0, 8, accel1);Serial.println("Lost_Connection");};
```

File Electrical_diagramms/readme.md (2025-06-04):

# Woodpecker 
## Electrical diagramms

### Accumulator batteries and 72V section:

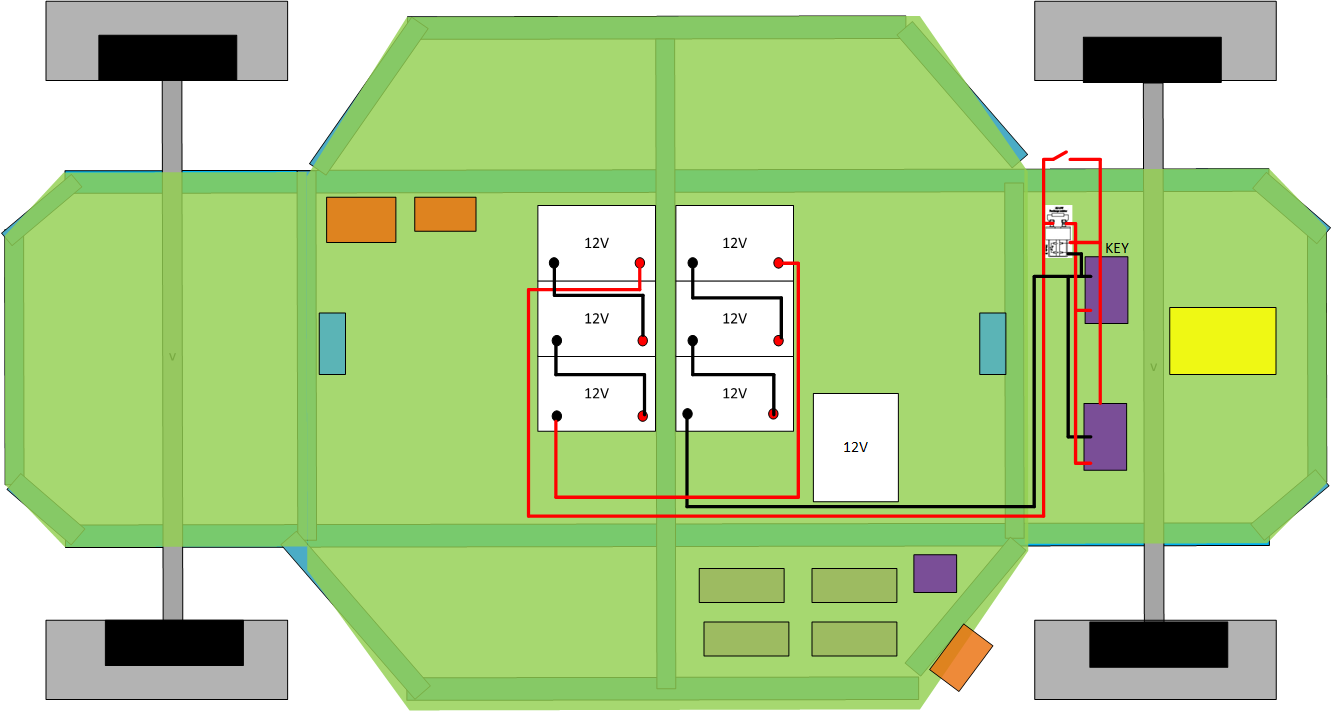
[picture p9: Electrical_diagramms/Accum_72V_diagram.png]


### 72V and 12V connections: 

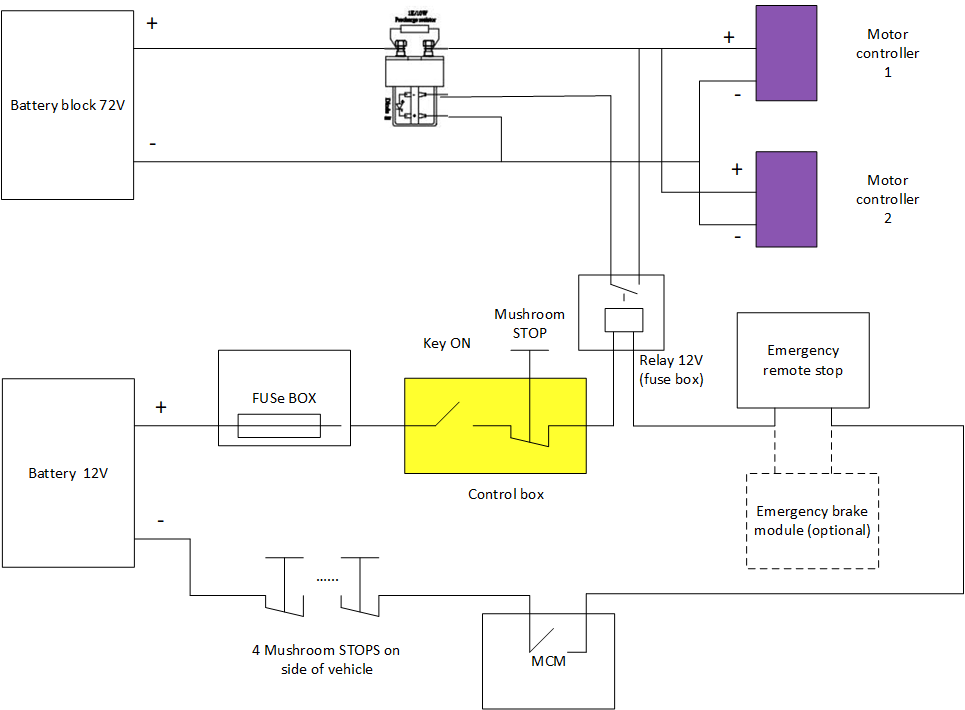
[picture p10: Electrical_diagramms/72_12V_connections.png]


### CAN and 12V networks: 

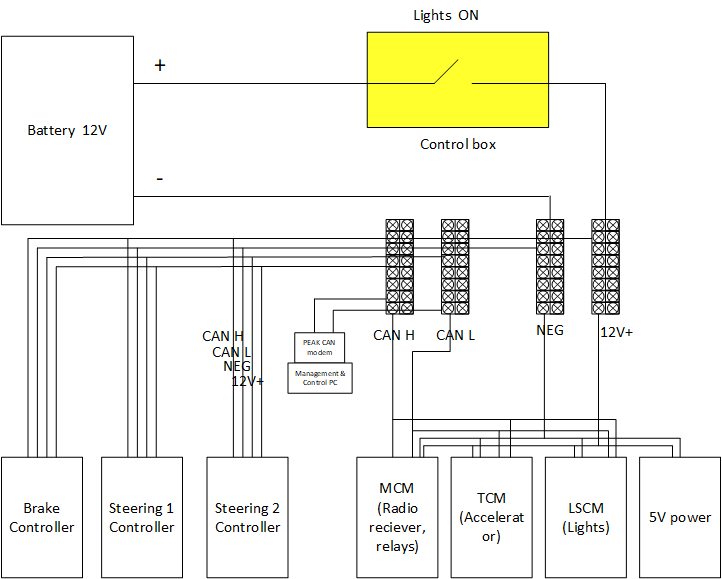
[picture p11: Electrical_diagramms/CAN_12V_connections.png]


### Motor Controller diagramm: 

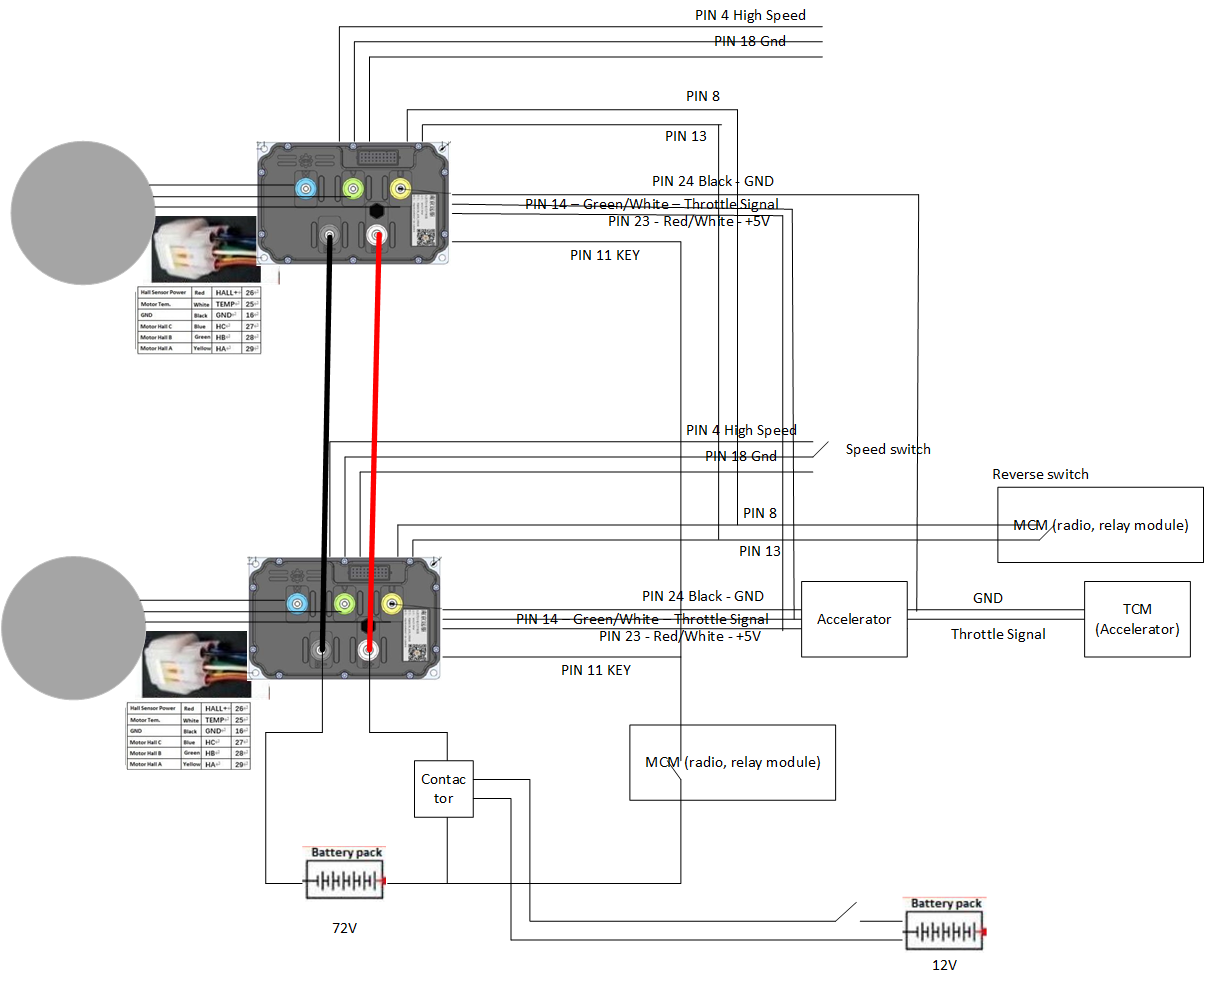
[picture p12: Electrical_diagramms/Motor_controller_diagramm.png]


### Motor controller diagremm for tests:
 
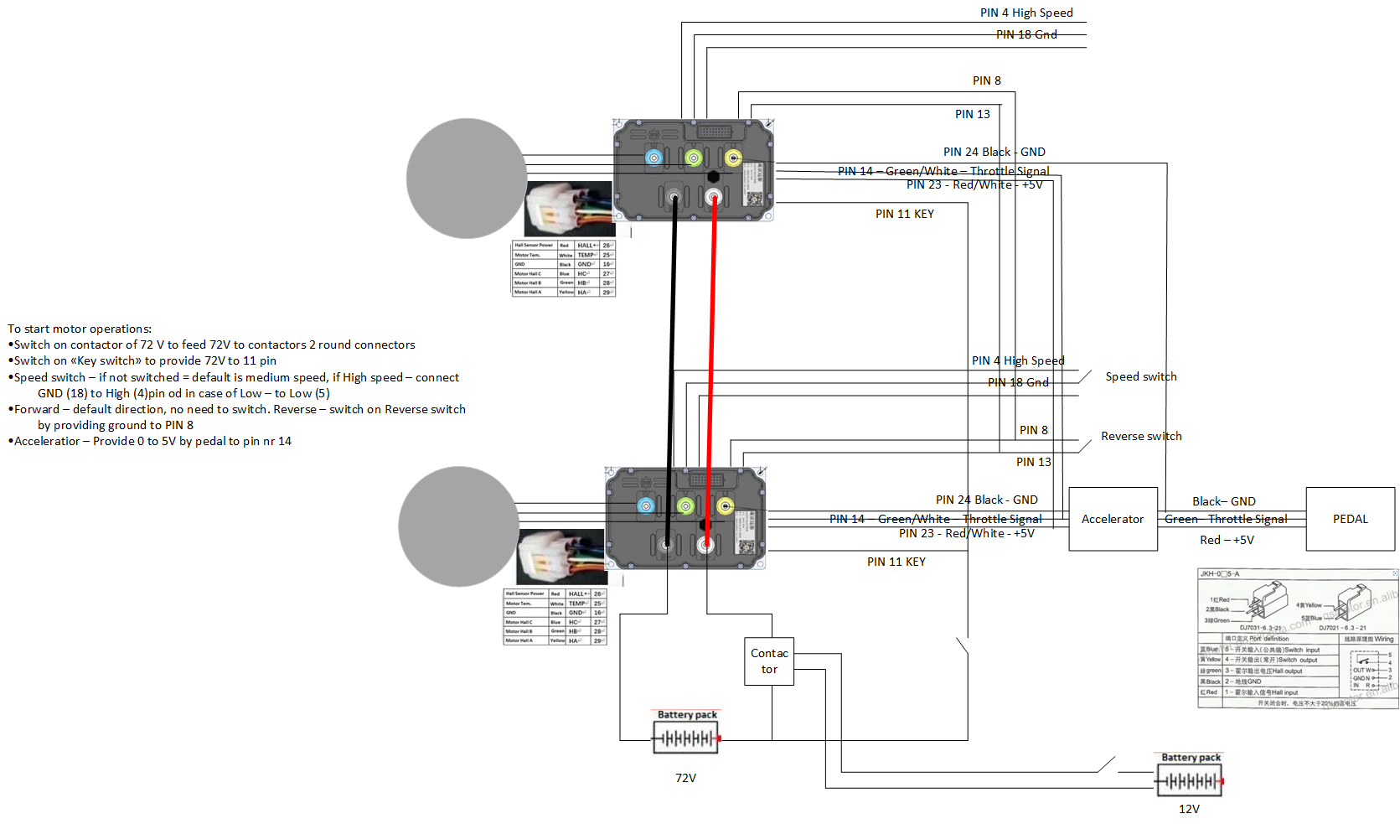
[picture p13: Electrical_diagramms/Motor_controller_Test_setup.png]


### Motor controller connection diagramm: 

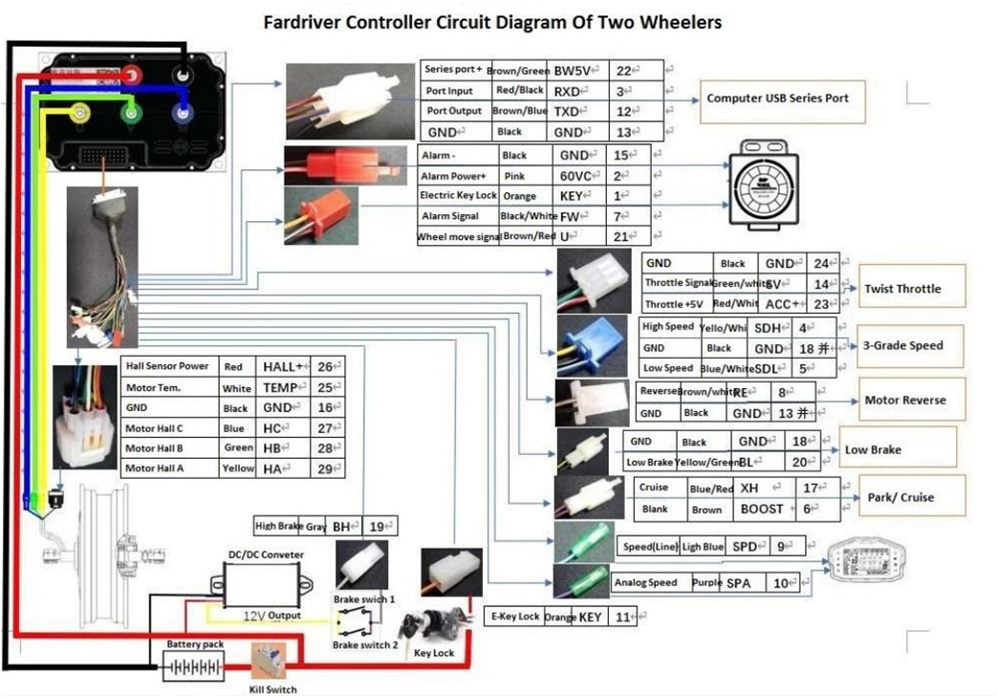
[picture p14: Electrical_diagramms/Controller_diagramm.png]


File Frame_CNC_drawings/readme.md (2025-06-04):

# Woodpecker 

## Frame CNC drawings

Frame is manuifactured from 3 different thickness plywood: 12, 45 and 50 mm

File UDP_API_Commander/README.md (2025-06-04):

# Commander API functions

Functions for control of car's actuators (steering, throttle, braking)

## Configuration

Set IP address and port number of commender node UDP server (in act.h file)

```
#define UDP_API_ADDR      "127.0.0.1"
#define UDP_API_PORT      8050
```

## set_throttle(Value)

Press throttle pedal to given position [0.0 ... 1.0].
(1.0 - pressed to maximum, 0.0 - released)

## set_breaking(Value)

Press braking pedal to given position [0.0 ... 1.0].
(1.0 - pressed to maximum, 0.0 - released)

## set_steering(Angle)

Position the car's front wheels to a given angle in degrees [-22.0 ... 22.0].
  - >0.0 - right
  - <0.0 - left
  - =0.0 - stright

## set_speed(Speed)

Drive the car at a given speed in km/h [0.0 ... 50.0].

## set_off()

Turn off all actuators.

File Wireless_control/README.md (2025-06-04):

# Woodpecker 2023 Wireless Operation

Operation with Open TX Taranis X9D remote control 

Open TX Companion download here https://www.open-tx.org/



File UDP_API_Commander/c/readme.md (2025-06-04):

#Drive By Wire UDP API command line tool

##Installation instructions

To compile run:
```
cd /home/pi/commander_api/c
gcc -o udpcli udpcli.c
```

To add the path permanently, add the following line at the end of ~/.bashrcfile
```
sudo nano ~/.bashrc
```
Add the below line at the end
```
export PATH=$PATH:/path/to/the/directory
```
like
```
export PATH=$PATH:/home/pi/commander_api/c
```

Use:
```
udpcli set steering 20  /// Set the steering value to 20 degrees
udpcli set braking 0.20   /// Set braking from 0  to 1
udpcli set throttle 0.20  /// Set throttle from 0 to 1
udpcli set speed 20
udpcli set off 
```

## set_throttle(Value)

Press throttle pedal to given position [0.0 ... 1.0].
(1.0 - pressed to maximum, 0.0 - released)

## set_breaking(Value)

Press braking pedal to given position [0.0 ... 1.0].
(1.0 - pressed to maximum, 0.0 - released)

## set_steering(Angle)

Position the car's front wheels to a given angle in degrees [-30.0 ... 30.0].
  - >0.0 - right
  - <0.0 - left
  - =0.0 - stright

## set_speed(Speed)

Drive the car at a given speed in km/h [0.0 ... 50.0].

## set_off()

Turn off all actuators.

#Monitoring

see the UDP packets on localhost
```
sudo tcpdump -i lo -n udp port 8050 -X
tcpdump -i lo udp port 8125 -vv -X
```
To show all UDP packets:
```
sudo tcpdump -n udp dst -i any portrange 8040-8060
```

To show listening UDP ports:
```
netstat -vaun
```

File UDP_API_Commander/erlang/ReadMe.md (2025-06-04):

#Erlang example compilation

Install Erlang:
```
sudo apt-get install erlang
```
Compile act.erl:
```
@: cd /home/commander_api/erlang
@: erl
Erlang/OTP 19 [erts-8.2.1] [source] [smp:4:4] [async-threads:10] [kernel-poll:false]
Eshell V8.2.1  (abort with ^G)
1> c(act).
{ok,act}
2>
```
As result act.beam should be created

The use:
```
@: erl
Erlang/OTP 19 [erts-8.2.1] [source] [smp:4:4] [async-threads:10] [kernel-poll:false]
Eshell V8.2.1  (abort with ^G)
1> act:set_steering(10).
[1,0,3,232]
ok
2>
```

Commands:
```
set_steering(Angle) ->
set_throttle(Val) ->
set_braking(Val) ->
set_speed(Speed) ->
set_off() ->
```

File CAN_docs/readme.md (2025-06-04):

# Woodpecker 
## CAN subsystem

Woodpecker project comprises Busmaster CAN software https://rbei-etas.github.io/busmaster/

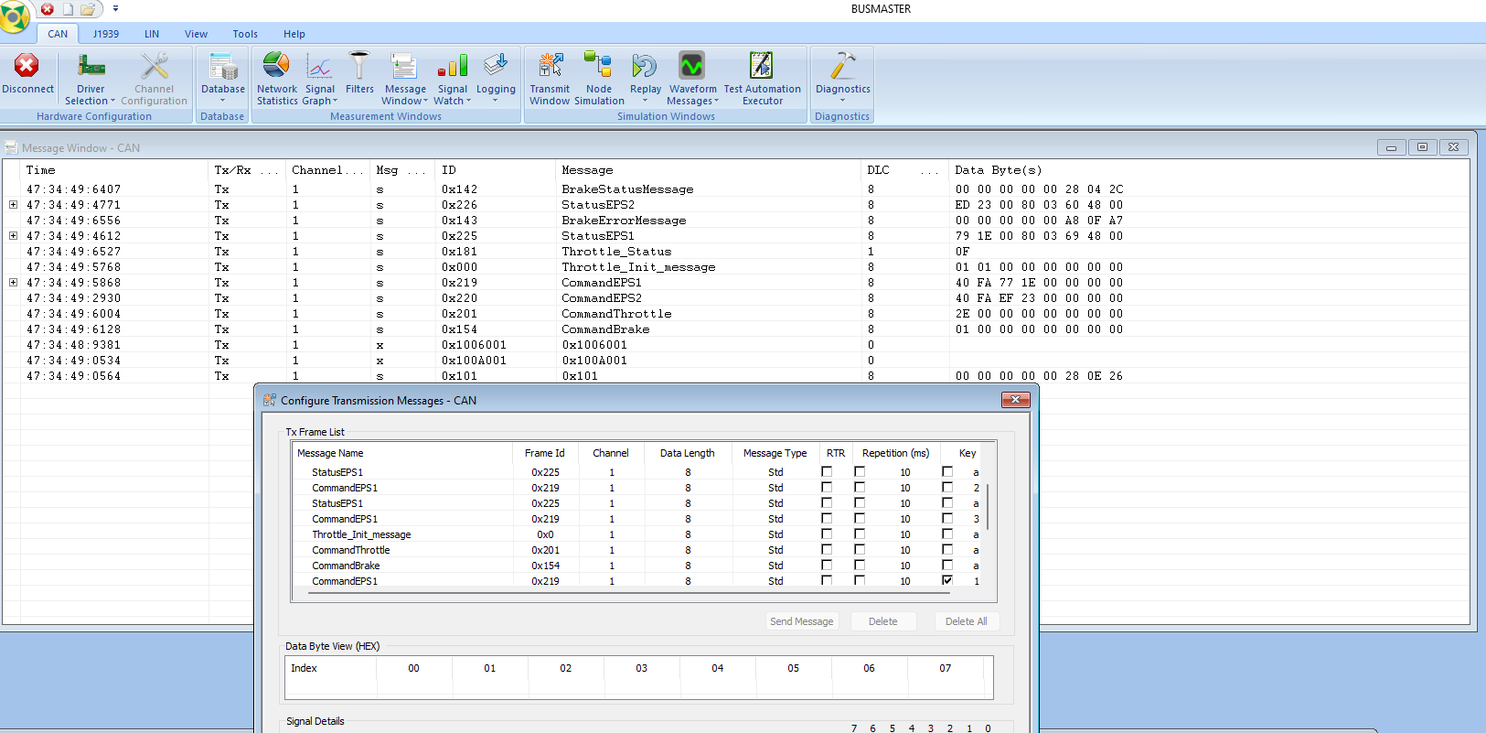
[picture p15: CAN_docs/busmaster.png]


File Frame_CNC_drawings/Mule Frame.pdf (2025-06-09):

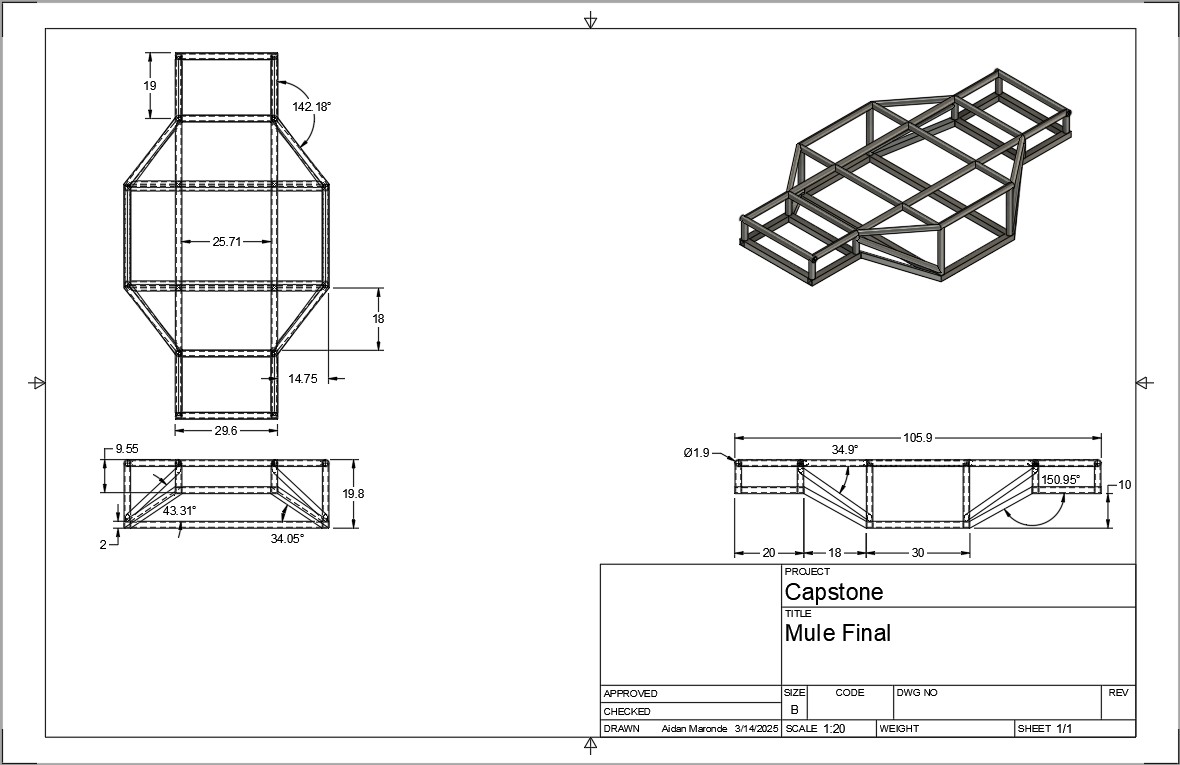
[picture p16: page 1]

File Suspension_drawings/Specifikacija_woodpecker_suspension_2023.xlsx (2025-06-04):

kods… | Apraksts | Mērv | GAB
900-100 | Flat_part_final_1_s235_3mm_8gb | GAB | 8
900-100 | MirrorMirrorU_bracket_final_rear_right_1_s235_3mm_2gb | GAB | 2
900-100 | MirrorU_bracket_final_front_right_1_s235_3mm_2gb | GAB | 2
900-100 | MirrorU_bracket_final_rear_left_1_s235_3mm_2gb | GAB | 2
900-100 | U_bracket_final_front_left_1_s235_3mm_2gb | GAB | 2
900-100 | arm_bracket_final_1_s235_5mm_32gb | GAB | 32
900-100 | Shock_bracket_final_1_s235_5mm_8gb | GAB | 8

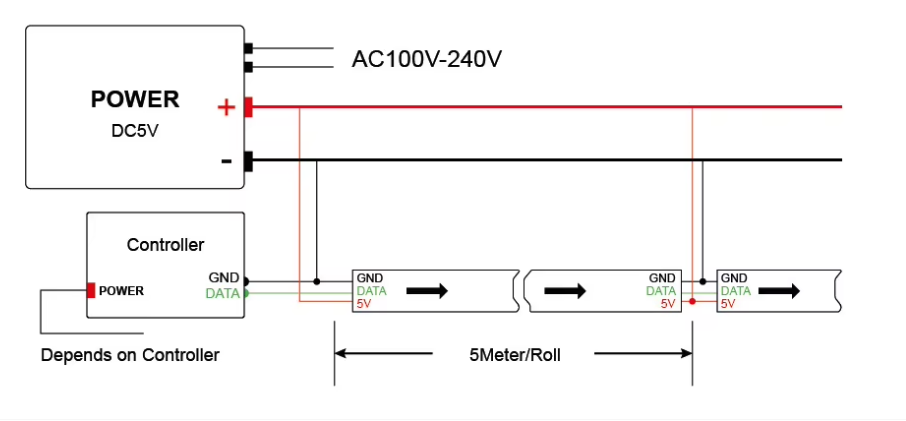
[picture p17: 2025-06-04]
Light_and_sound_controller/Diagramm_light_strip_WS.png

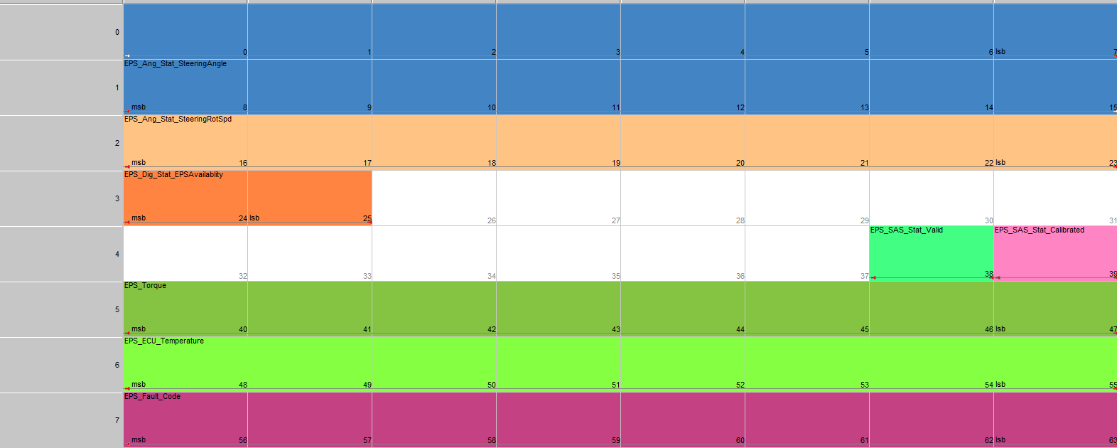
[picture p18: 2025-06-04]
Steering_controller/Steering_CAN_message_structure.png

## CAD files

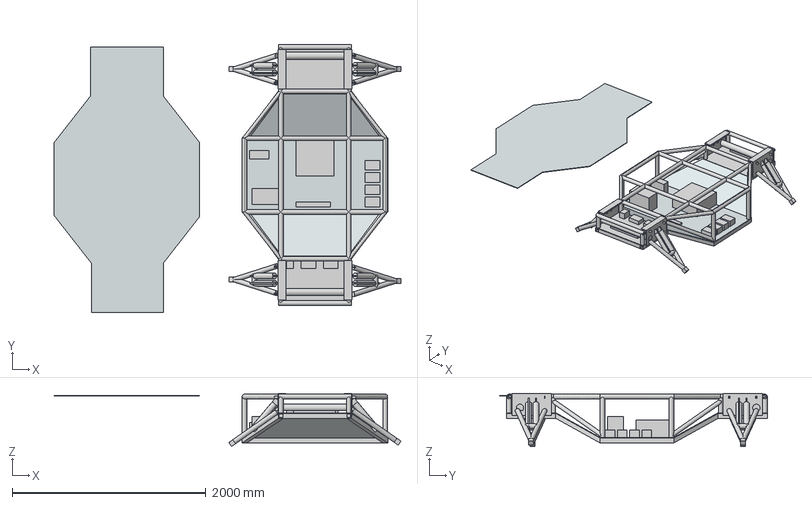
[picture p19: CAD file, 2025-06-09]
Frame_CNC_drawings/Mule Full Assembly.step
3580.3 x 2764.0 x 547.9 mm
Mule Final
Bottom Cover 2 (1) x 2
Bottom Cover 3 (1)
Top Cover Whole (1)
Bottom Cover F
Bottom Cover B
Motor Batteries
Computer Systems
Computer Batteries
Wire Harness
Motor Controllers
Connector
Wheel Bracket x 4
Steering x 2
Steering (1) x 2
Brake Fluid Reseevoir
Bottom Bar x 4
Shocks x 2
Shocks v2(Mirror) x 2

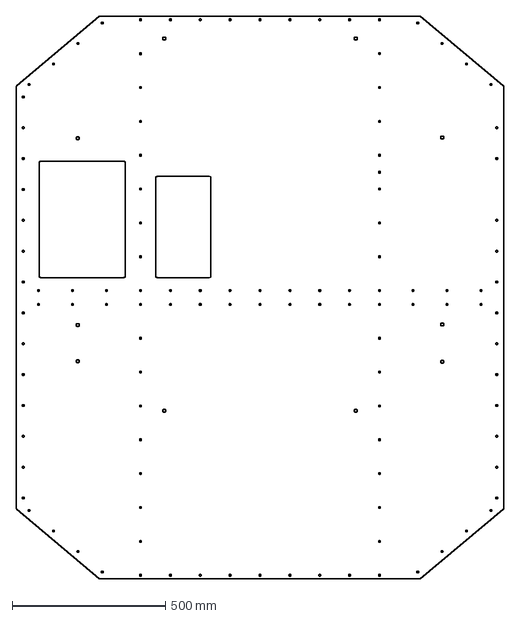
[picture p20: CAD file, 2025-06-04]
Frame_CNC_drawings/12mm/CovertopCenter-1gab.DXF
1589.9 x 1835.0 mm

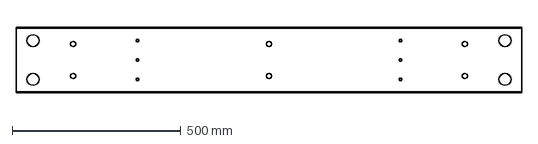
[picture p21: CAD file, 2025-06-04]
Frame_CNC_drawings/45mm/Crossbar-2gab (Left_view).DXF
1500.0 x 195.0 mm

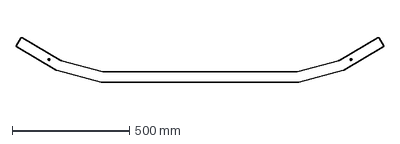
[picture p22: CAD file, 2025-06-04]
Frame_CNC_drawings/50mm/Bumper_top_bottom-4gab.DXF
1570.6 x 192.0 mm

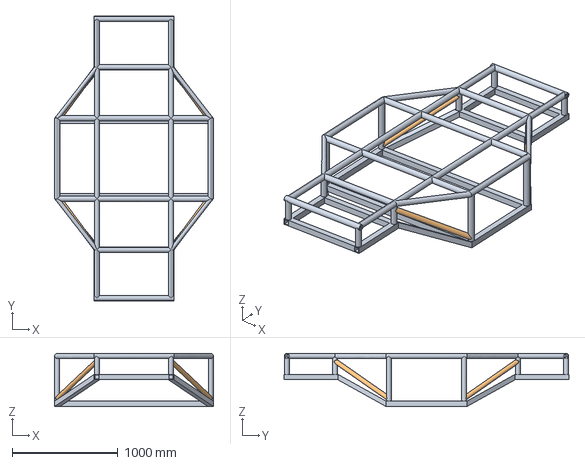
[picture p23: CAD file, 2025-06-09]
Frame_CNC_drawings/Mule Final v4.step
1503.7 x 2692.4 x 502.9 mm

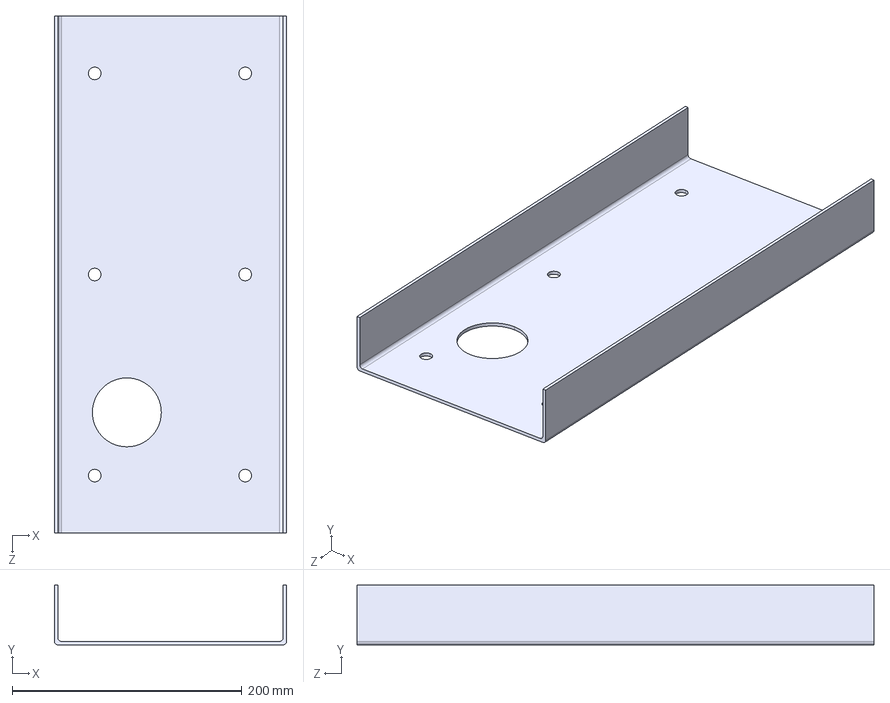
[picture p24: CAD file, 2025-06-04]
Suspension_drawings/MirrorMirrorU_bracket_final_rear_right_1.STEP
202.0 x 52.0 x 450.0 mm

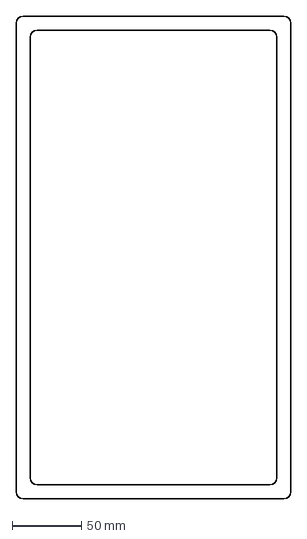
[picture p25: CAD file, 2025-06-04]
Frame_CNC_drawings/12mm/Accu_cover-1gab.DXF
198.0 x 348.0 mm

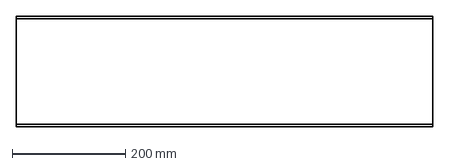
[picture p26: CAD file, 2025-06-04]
Frame_CNC_drawings/45mm/Short_cross-(Right_view).DXF
735.0 x 195.0 mm

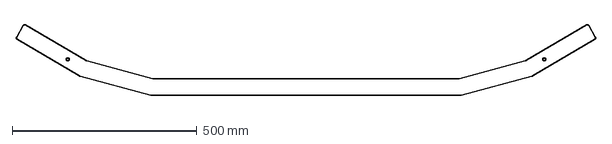
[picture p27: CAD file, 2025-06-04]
Frame_CNC_drawings/50mm/Bumper_center-4gab.DXF
1570.6 x 192.0 mm

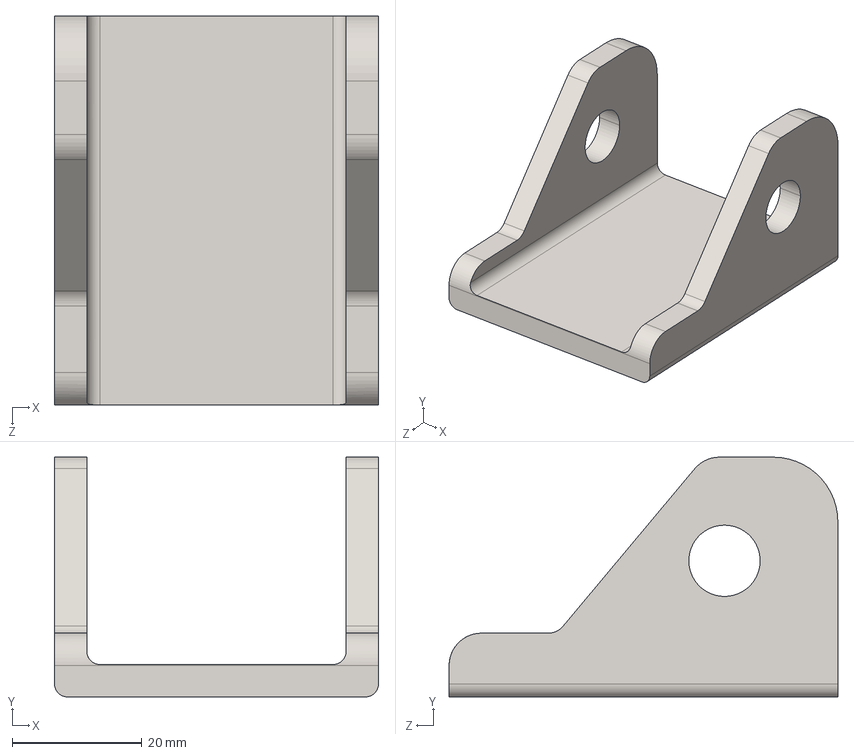
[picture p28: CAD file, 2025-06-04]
Suspension_drawings/Shock_bracket_final_1.STEP
50.0 x 37.0 x 60.0 mm

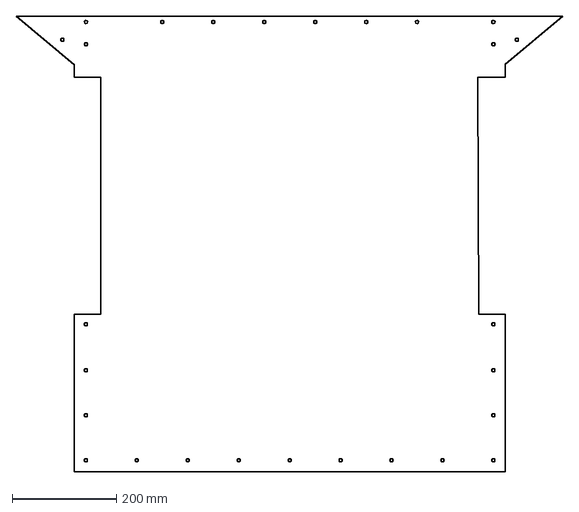
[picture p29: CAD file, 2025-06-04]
Frame_CNC_drawings/12mm/CoverEnd-4gab.DXF
1046.9 x 872.5 mm

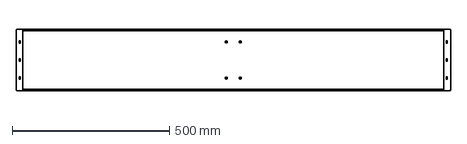
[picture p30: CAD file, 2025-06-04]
Frame_CNC_drawings/45mm/Side-2gab (Left_view).DXF
1380.0 x 195.0 mm

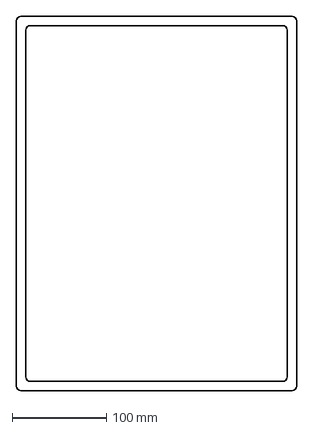
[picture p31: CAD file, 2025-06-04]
Frame_CNC_drawings/12mm/Small_cover-1gab.DXF
298.0 x 398.0 mm

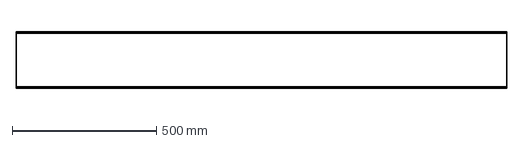
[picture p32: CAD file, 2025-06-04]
Frame_CNC_drawings/45mm/Long_final (Right_view).DXF
1700.0 x 195.0 mm

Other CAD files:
Suspension_drawings/MirrorU_bracket_final_rear_left_1.STEP
Suspension_drawings/arm_bracket_final_1.STEP
Frame_CNC_drawings/12mm/CoverBottomCenter-1gab.DXF
Frame_CNC_drawings/45mm/Side_langle (Right_view).DXF
Frame_CNC_drawings/45mm/Crossbar (Right_view).DXF
Frame_CNC_drawings/45mm/Long_final-4gab (Left_view).DXF
Frame_CNC_drawings/45mm/Short_cross-2gab (Left_view).DXF
Frame_CNC_drawings/45mm/Side (Right_view).DXF
Frame_CNC_drawings/45mm/Side_angle-4gab (Left_view).DXF
Suspension_drawings/Bracket_U.STEP
Suspension_drawings/Flat_part_final_1.STEP
Suspension_drawings/MirrorU_bracket_final_front_right_1.STEP
Suspension_drawings/Paraugs_vienam_komplektam_4gb.STEP
Suspension_drawings/U_bracket_final_front_left_1.STEP

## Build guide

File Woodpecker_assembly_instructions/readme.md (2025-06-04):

# Woodpecker 
## Woodpecker assembly instructions

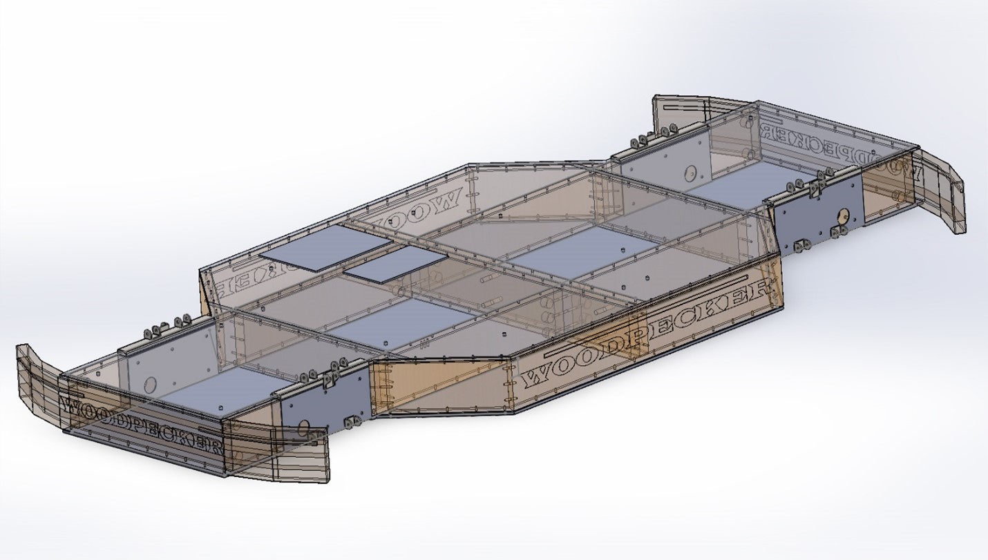
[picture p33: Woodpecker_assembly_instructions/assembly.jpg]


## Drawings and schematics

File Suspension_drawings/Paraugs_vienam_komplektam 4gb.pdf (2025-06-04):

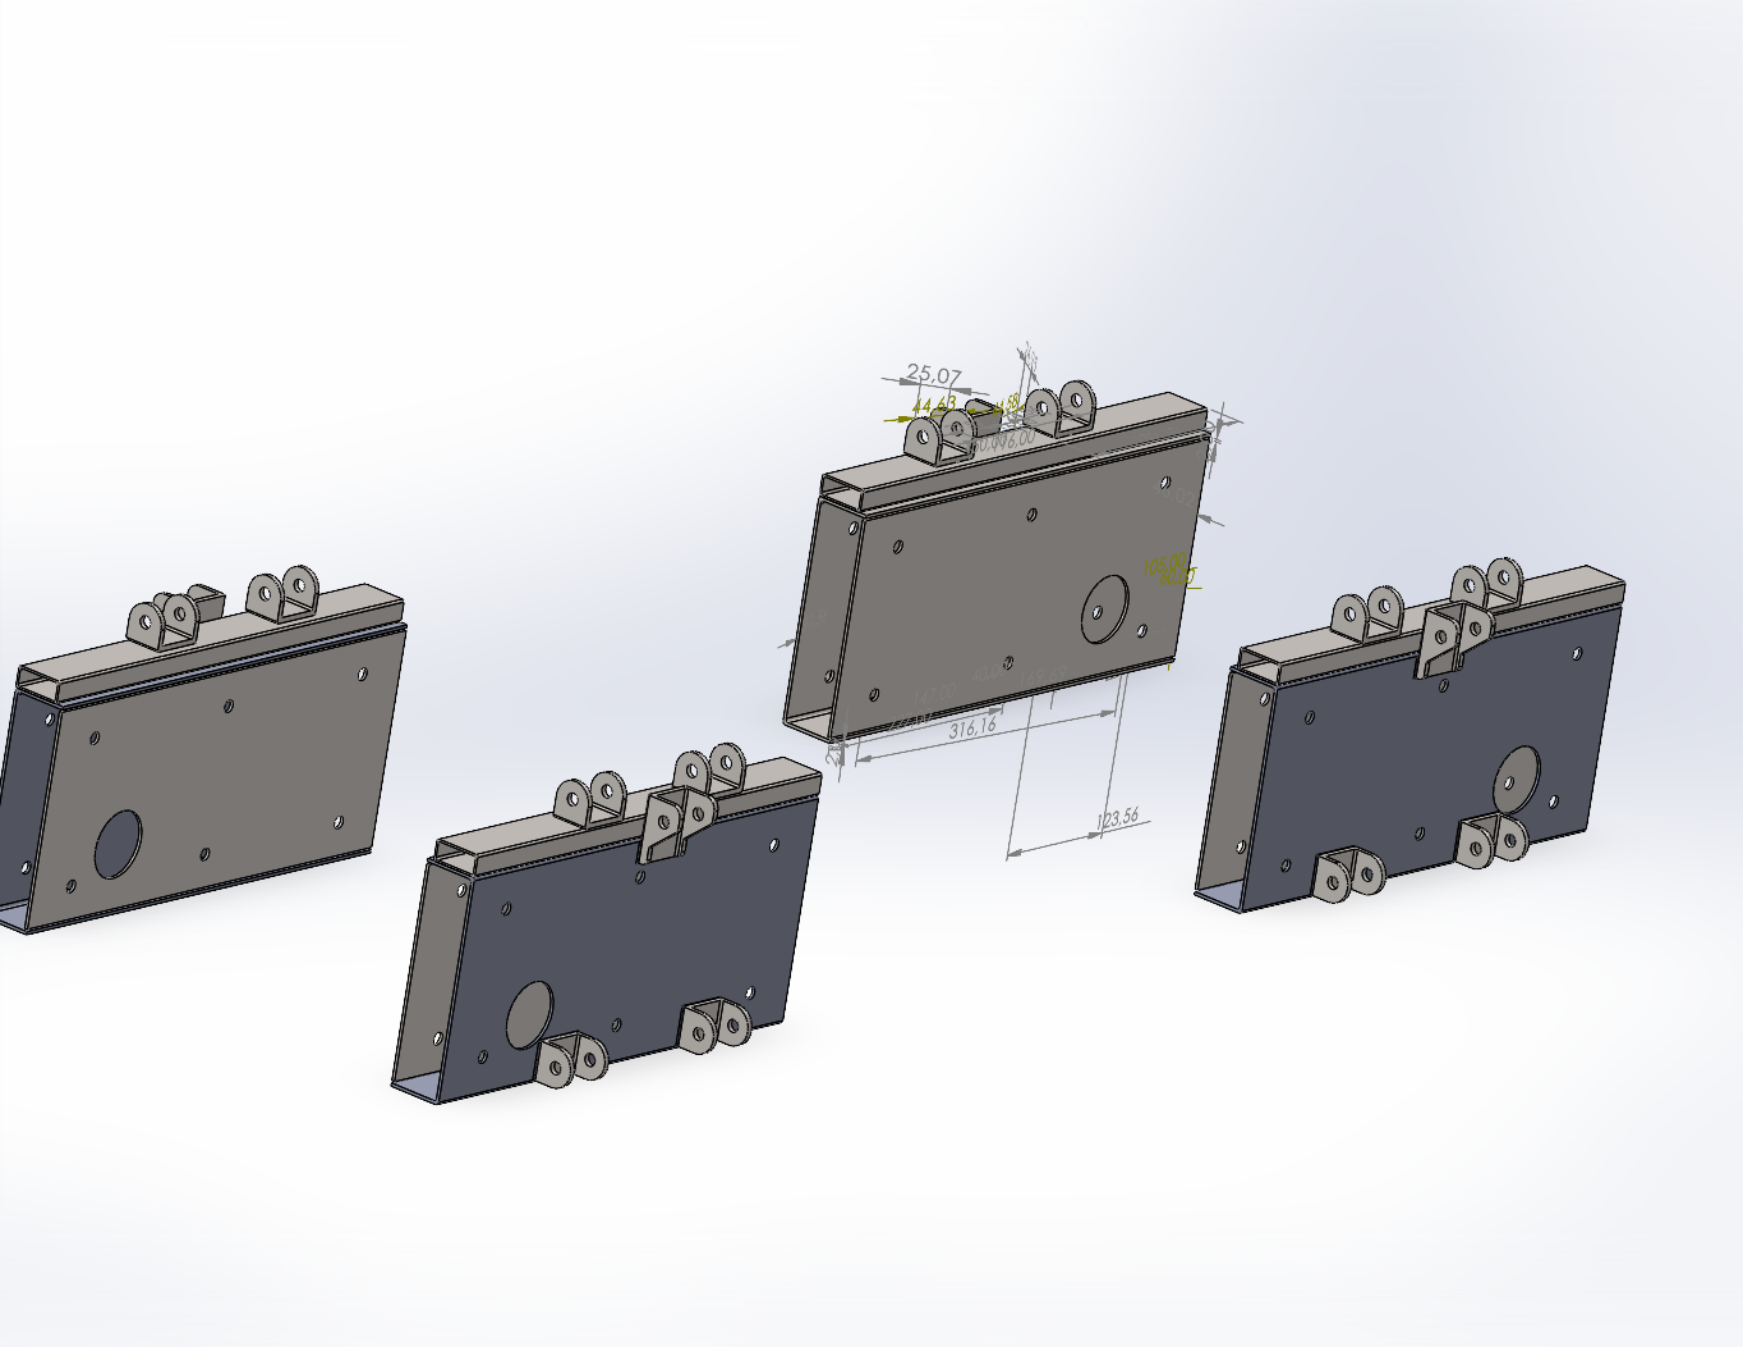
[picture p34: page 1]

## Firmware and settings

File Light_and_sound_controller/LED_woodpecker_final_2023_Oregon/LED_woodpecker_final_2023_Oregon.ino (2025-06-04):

#include <can-serial.h>
#include <mcp2515_can.h>
#include <mcp2515_can_dfs.h>
#include <mcp2518fd_can.h>
#include <mcp2518fd_can_dfs.h>
#include <mcp_can.h>

// Woodpecker  http://woodpeck.org
// PIN Numbers
//

// PIN 3 LED strip Front Left
// PIN 4 LED strip Right
// PIN 5 LED strip Left
// PIN 6 LED strip Rear Right
// PIN 9 CAN
// PIN 11 LED strip Front Right
// PIN 12 LED strip Rear Left
// PIN 13 Sound Buzzer
// PIN 22 External Relay  - Low Beam       - 0
// PIN 24 External Relay  - High Beam      - 1
// PIN 26 External Relay -  DRL            - 2
// PIN 28 External Relay - Right Turn      - 3 
// PIN 30 External Relay - Left Turn       - 4 
// PIN 32 External Relay  - Brakes -       - 5
// PIN 34 External Relay  - Reverse Lights - 6
// PIN 36 External Relay  - Horn -         - 7


#include <Adafruit_NeoPixel.h>
#include <mcp_can.h>
#include <SPI.h>

#define NUM_LEDS1 72
#define NUM_LEDS2 72
#define NUM_LEDS3 144
#define NUM_LEDS4 144
#define NUM_LEDS5 72
#define NUM_LEDS6 72

//#define PIN1 11  // Front Right
//#define PIN2 3  // Front Left
//#define PIN3 4  // Right
//#define PIN4 5  // Left
//#define PIN5 6  // Rear Right
//#define PIN6 12  // Rear Left
#define PIN1 47  // Front Right
#define PIN2 44 // Front Left
#define PIN3 46  // Right
#define PIN4 45 // Left
#define PIN5 48 // Rear Right
#define PIN6 49  // Rear Left
int piezoPin = 13; //Sound buzzer
byte relayPin[8] = {    //Relay module pins
  22,24,26,28,30,32,34,36};
const int SPI_CS_PIN = 9; //CANbus module 
unsigned char Distance1m[8] = {0x00, 0x00, 0x00, 0x00, 0x00, 0x00, 0x00, 0x09};

MCP_CAN CAN(SPI_CS_PIN);                                    // Set CS pin
const int ledHIGH    = 1;
const int ledLOW     = 0;
unsigned char stmp[8] = {ledHIGH, 1, 2, 3, ledLOW, 5, 6, 7};


#define NUMPIXELS1 72
#define NUMPIXELS2 72
#define NUMPIXELS3 144
#define NUMPIXELS4 144
#define NUMPIXELS5 72
#define NUMPIXELS6 72

Adafruit_NeoPixel strip1 = Adafruit_NeoPixel(NUMPIXELS1, PIN1, NEO_GRB + NEO_KHZ800);
Adafruit_NeoPixel strip2 = Adafruit_NeoPixel(NUMPIXELS2, PIN2, NEO_GRB + NEO_KHZ800);
Adafruit_NeoPixel strip3 = Adafruit_NeoPixel(NUMPIXELS3, PIN3, NEO_GRB + NEO_KHZ800);
Adafruit_NeoPixel strip4 = Adafruit_NeoPixel(NUMPIXELS4, PIN4, NEO_GRB + NEO_KHZ800);
Adafruit_NeoPixel strip5 = Adafruit_NeoPixel(NUMPIXELS5, PIN5, NEO_GRB + NEO_KHZ800);
Adafruit_NeoPixel strip6 = Adafruit_NeoPixel(NUMPIXELS6, PIN6, NEO_GRB + NEO_KHZ800);

uint32_t white = strip1.Color(255, 255, 255);
uint32_t blue = strip1.Color(0, 0, 255);
uint32_t red = strip1.Color(255, 0, 0);
uint32_t orange = strip1.Color(255, 165, 0);
uint32_t yellow = strip1.Color(255, 255, 0);
uint32_t nocolor = strip1.Color(0, 0, 0);
int orangeHUE = 6000;
int yellowHUE = 9000;

// strip.setPixelColor(i, strip.gamma32(strip.ColorHSV(pixelHue)));

int count = 1;  //For initialization show run
#define DELAYVAL 1 // Time (in milliseconds) to pause between pixels

#define INT32U unsigned long int
INT32U canId = 0x101;
unsigned char len = 0;
unsigned char buf[8];
char str[20];
String command;
String CanMessage="";

int LeftTurnState=0;
int RightTurnState=0;
int HazardState=0;
int LowBeamState=0;
int HighBeamState=0;
int BrakeLightState=0;
int DRLState=0;

void setup() {
  // initialize serial communication:
  Serial.begin(115200);
  for(int i = 0; i < 8; i++)  pinMode(relayPin[i],OUTPUT);
  for(int j = 0; j < 8; j++)  digitalWrite(relayPin[j],HIGH);
  strip1.begin();
  strip1.show();
  strip2.begin();
  strip2.show();
  strip3.begin();
  strip3.show();
  strip4.begin();
  strip4.show();
  strip5.begin();
  strip5.show();
  strip6.begin();
  strip6.show();
  ClearAllLeds();
//  demorun();   
 Initialization(0, 0, 250, 8, 1000, 0);
 ClearAllLeds ();
  while (CAN_OK != CAN.begin(CAN_500KBPS))              // init can bus : baudrate = 500k
   {
       Serial.println("CAN BUS Shield init fail");
        Serial.println(" Init CAN BUS Shield again");
        delay(100);
    }
   Serial.println("CAN BUS Shield init ok!");
}

 
 void loop() {
 //    demorun(); 
       //                         Serial.println("LeftTurnState, RightTurnState, HazardState, LowBeamState, HighBeamState, BrakeLightState, DRLState");
       //                         Serial.print(LeftTurnState);
       //                         Serial.print(RightTurnState);
       //                         Serial.print(HazardState);
       //                         Serial.print(LowBeamState);
       //                         Serial.print(HighBeamState);
       //                         Serial.print(BrakeLightState);
       //                         Serial.print(DRLState);
       //                         Serial.println();
     CAN.sendMsgBuf(0x401, 0, 8, Distance1m);                                       
                               if (Serial.available() > 0) {
                                  int inByte = Serial.read();
                              
                                   switch (inByte) {
                                     case '0':
                                      Serial.println("Switch OFF");
                                     ClearAllLedsandRelays();
                                     break;  
                                     case '1':
                                      Serial.println("Front Right Test");
                                       strip1.setBrightness(80);
                                       setAll1(255, 255, 255);
                                       strip1.show();
                                     break;
                                     case '2':
                                      Serial.println("Front Left Test");
                                       strip2.setBrightness(80);
                                       setAll2(255, 255, 255);
                                       strip2.show();
                                     break;
                                     case '3':
                                      Serial.println("Right Test");
                                       strip3.setBrightness(80);
                                       setAll3(255, 255, 255);
                                       strip3.show();
                                     break;  
                                     case '4':
                                       Serial.println("Left Test");
                                       strip4.setBrightness(80);
                                       setAll4(255, 255, 255);
                                       strip4.show();
                                     break;  
                                     case '5':
                                       Serial.println("Rear Right Test");
                                       strip5.setBrightness(80);
                                       setAll5(255, 255, 255);
                                       strip5.show();
                                     break;  
                                     case '6':
                                       Serial.println("Rear Left Test");
                                       strip6.setBrightness(80);
                                       setAll6(255, 255, 255);
                                       strip6.show();
                                     break; 
                                     case '7':
                                      Serial.println("Strobe White");
                                          // Strobe - Color (red, green, blue), number of flashes, flash speed, end pause
                                              StrobeLeft(255, 255, 255, 5, 40, 100); //White
                                              StrobeRight(255, 255, 255, 5, 40, 100); //White
                                              StrobeLeft(255, 255, 255, 5, 40, 100); //White
                                              StrobeRight(255, 255, 255, 5, 40, 100); //White
                                              StrobeLeft(255, 255, 255, 5, 40, 100); //White
                                              StrobeRight(255, 255, 255, 5, 40, 100); //White
                                              StrobeLeft(255, 255, 255, 5, 40, 100); //White
                                              StrobeRight(255, 255, 255, 5, 40, 100); //White
                              
                                     break;
                                     case '8':
                                      Serial.println("Strobe Police Blue");
                                          // Strobe - Color (red, green, blue), number of flashes, flash speed, end pause
                                              StrobeLeft(0, 0, 255, 5, 40, 100); //Blue
                                              StrobeRight(0, 0, 255, 5, 40, 100); //Blue
                                              StrobeLeft(0, 0, 255, 5, 40, 100); //Blue
                                              StrobeRight(0, 0, 255, 5, 40, 100); //Blue
                                              StrobeLeft(0, 0, 255, 5, 40, 100); //Blue
                                              StrobeRight(0, 0, 255, 5, 40, 100); //Blue
                                              StrobeLeft(0, 0, 255, 5, 40, 100); //Blue
                                              StrobeRight(0, 0, 255, 5, 40, 100); //Blue
                                     break;
                                     case '9':
                                      Serial.println("Set Brakes Front");
                                       ClearLights1();
                                       ClearLights2();
                                       strip1.setBrightness(255);
                                       setAll1(255, 0, 0);
                                       strip2.setBrightness(255);
                                       setAll2(255, 0, 0);
                                       break;
                                     case 'p':
                                      Serial.println("Set All Orange");
                                       ClearLights1();
                                       ClearLights2();
                                       ClearLights3();
                                       ClearLights4();
                                       ClearLights5();
                                       ClearLights6();
                                       strip1.setBrightness(255);
                                       setAll1(255, 165, 0);
                                       strip2.setBrightness(255);
                                       setAll2(255, 165, 0);
                                       strip3.setBrightness(255);
                                       setAll3(255, 165, 0);
                                       strip4.setBrightness(255);
                                       setAll4(255, 165, 0);
                                       strip5.setBrightness(255);
                                       setAll5(255, 165, 0);
                                       strip6.setBrightness(255);
                                       setAll6(255, 165, 0);
                                       break;
                                     case 'q':
                                      Serial.println("Hazard ON");
                                          setAll1(0,0,0);
                                          setAll2(0,0,0);
                                          setAll5(0,0,0);
                                          setAll6(0,0,0);
                                       strip1.setBrightness(255);
                                       setAll1(255, 165, 0);
                                       strip2.setBrightness(255);
                                       setAll2(255, 165, 0);
                                       strip5.setBrightness(255);
                                       setAll5(255, 165, 0);
                                       strip6.setBrightness(255);
                                       setAll6(255, 165, 0);
                                       delay(3000);
                                          setAll1(0,0,0);
                                          setAll2(0,0,0);
                                          setAll5(0,0,0);
                                          setAll6(0,0,0);
                                        strip1.setBrightness(255);
                                       setAll1(255, 165, 0);
                                       strip2.setBrightness(255);
                                       setAll2(255, 165, 0);
                                       strip5.setBrightness(255);
                                       setAll5(255, 165, 0);
                                       strip6.setBrightness(255);
                                       setAll6(255, 165, 0);   
                                                delay(3000);
                                          setAll1(0,0,0);
                                          setAll2(0,0,0);
                                          setAll5(0,0,0);
                                          setAll6(0,0,0);
                                        strip1.setBrightness(255);
                                       setAll1(255, 165, 0);
                                       strip2.setBrightness(255);
                                       setAll2(255, 165, 0);
                                       strip5.setBrightness(255);
                                       setAll5(255, 165, 0);
                                       strip6.setBrightness(255);
                                       setAll6(255, 165, 0);          
                                       break;
                                       case 'w':
                                      Serial.println("Turn Signal Right");
                                      count = 5;
                                      turnsignalright();
                                       break;
                                      case 'e':
                                      Serial.println("Turn Signal Left");
                                      count = 5;
                                      turnsignalleft();
                                       break;
                                      case 'r':
                                      Serial.println("Hazard");
                                      count = 5;
                                      turnsignalhazard();
                                       break;
                                     case 't':
                                      Serial.println("Running Lights Front");
                                      runninglightsfront();
                                       break;
                                     case 'y':
                                      Serial.println("Running Lights Rear");
                                      runninglightsraer();
                                       break;
                                     case 'u':
                                      Serial.println("Brakes Rear");
                                      brakesrear();
                                      break;
                                     case 'i':
                                      Serial.println("Brakes Front");
                                      brakesfront();
                                      break;
                                     case 'o':
                                      Serial.println("Danger");
                                      Danger(255, 255, 0, 4, 40, 100);
                                      delay(500);
                                      Danger(255, 255, 0, 4, 40, 100);
                                      delay(500);
                                      Danger(255, 255, 0, 4, 40, 100);
                                      delay(500);
                                      Danger(255, 255, 0, 4, 40, 100);
                                      delay(500);
                                      Danger(255, 255, 0, 4, 40, 100);
                                      delay(500);
                                      Danger(255, 255, 0, 4, 40, 100);
                                      delay(500);
                                      Danger(255, 255, 0, 4, 40, 100);
                                      delay(500);
                                      Danger(255, 255, 0, 4, 40, 100);
                                      delay(500);
                                      break;
                                     case 'z':
                                      Serial.println("Buzzer 1");
                                        initsound();
                                      break;
                                      case 'x':
                                      Serial.println("Buzzer 2");
                                      backupsound();
                                       break;  
                                      case 'c':
                                      Serial.println("Low Beams ON");
                                      lowbeamON();
                                       break; 
                                      case 'v':
                                      Serial.println("Low Beams OFF");
                                      lowbeamOFF();
                                       break;  
                                     case 'b':
                                      Serial.println("High Beams ON");
                                      highbeamON();
                                       break; 
                                      case 'n':
                                      Serial.println("High Beams OFF");
                                      highbeamOFF();
                                       break;  
                                      case 'm':
                                      Serial.println("DEMO Run");
                                       demorun();   
                                       break;  
                                     case 'a':
                                      Serial.println("Reverse ON");
                                       reverselightsON();   
                                       break;
                                     case 's':
                                      Serial.println("Horn ON");
                                       hornON();
                                       delay (200);  
                                       Serial.println("Horn OFF");
                                       hornOFF();
                                       break;
                                     case 'd':
                                      Serial.println("Relay Test");
                                       digitalWrite(relayPin[0],LOW);
                                       delay (500); 
                                       digitalWrite(relayPin[0],HIGH);
                                       delay (500);                                        
                                       digitalWrite(relayPin[1],LOW);
                                       delay (500); 
                                       digitalWrite(relayPin[1],HIGH); 
                                       delay (500);                                      
                                       digitalWrite(relayPin[2],LOW);
                                       delay (500); 
                                       digitalWrite(relayPin[2],HIGH);
                                       delay (500);                           
                                       digitalWrite(relayPin[3],LOW);
                                       delay (500); 
                                       digitalWrite(relayPin[3],HIGH);  
                                       delay (500);                                      
                                       digitalWrite(relayPin[4],LOW);
                                       delay (500); 
                                       digitalWrite(relayPin[4],HIGH);
                                       delay (500);                                        
                                       digitalWrite(relayPin[5],LOW);
                                       delay (500); 
                                       digitalWrite(relayPin[5],HIGH);
                                       delay (500);                                        
                                       digitalWrite(relayPin[6],LOW);
                                       delay (500); 
                                       digitalWrite(relayPin[6],HIGH);
                                       delay (500);                                        
                                       digitalWrite(relayPin[7],LOW);
                                       delay (500);  
                                       digitalWrite(relayPin[7],HIGH);
                                       break;
                                      }
                              }
                              }


// ***************************************
// Clear Lights ///
// ***************************************

void ClearLights1() {
  for (int i = 0; i < strip1.numPixels(); i = i + 1) {
    strip1.setPixelColor(i, 0);    //turn every pixel off
  }
  strip1.show();
}

void ClearLights2() {
  for (int i = 0; i < strip1.numPixels(); i = i + 1) {
    strip2.setPixelColor(i, 0);    //turn every pixel off
  }
  strip2.show();
}

void ClearLights3() {
  for (int i = 0; i < strip1.numPixels(); i = i + 1) {
    strip3.setPixelColor(i, 0);    //turn every pixel off
  }
  strip3.show();
}

void ClearLights4() {
  for (int i = 0; i < strip1.numPixels(); i = i + 1) {
    strip4.setPixelColor(i, 0);    //turn every pixel off
  }
  strip4.show();
}

void ClearLights5() {
  for (int i = 0; i < strip1.numPixels(); i = i + 1) {
    strip5.setPixelColor(i, 0);    //turn every pixel off
  }
  strip5.show();
}
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

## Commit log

2025-06-04 next folder update
    [DBS_CAN_messages_calculations.xlsx]
2025-06-04 all folder uploads
    [Accu_cover-1gab.DXF, Bracket_U.STEP, Bumper_center-4gab.DXF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]
